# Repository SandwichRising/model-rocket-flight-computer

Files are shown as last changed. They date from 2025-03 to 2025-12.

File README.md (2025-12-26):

# Model Rocket Flight Control Computer
#### Servo-based flight control providing active stability and data logging for model rockets.

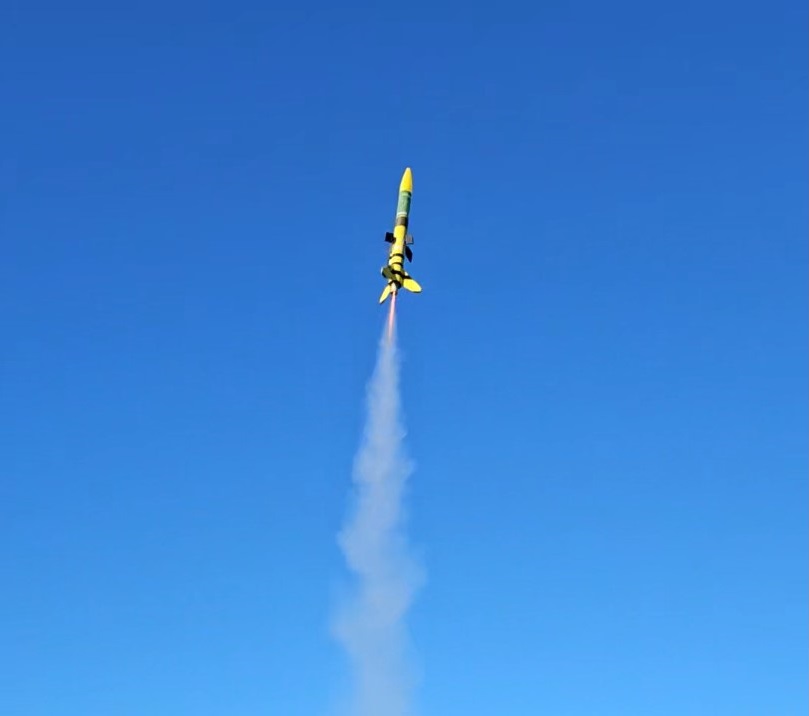
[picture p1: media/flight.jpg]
Model Rocket Flying


## Project Scope

This project is intended to provide hobbyists, academics, and model rocket teams with an understandable yet feature-rich open-source flight computer design utilizing servo-driven active stability and data logging capabilities. Block diagrams, schematics, source code, and engineering philosophies behind the design are all provided for anyone interested in model rocketry. Readily available consumer parts have been selected for the electronics and hobbyist rocket kits chosen with 3D-printed modifications added for ease of construction. The design is modular and made to be easily customized and edited, and also intended to be usable for steerable canards, tail fins, or thrust vector control (however, the latter two have not yet been tested). The implemented flight stability keeps the rocket pointed vertically by steering away from gravity, but does not allow any form of targeting or guidance to a target. 

To make this project hands-on and iterative, some unconventional decisions have been made that readers should be aware of, such as: choosing and constructing a theoretically conservative steering design using static modeling instead of fully modeling flight dynamics beforehand; using sensor fusion output that is not meant for thrust for the initial steering design, which is expected to need replacement under high-g forces; and using protoboard and CNC-milled PCB prototypes which are bulkier than factory-fabricated PCBs but allow rapid testing and design changes. It is my intent to continually analyze flight recordings to characterize the steering of different airframes and implement different state-space models to enhance the steering over time.

## Versioning

The project scope is divided into versions which contain an increasing number of features on varying rocket airframes. Currently, V1 and V2 are completed and have flight data recorded from numerous launches to analyze the active flight control behavior. Future versions with additional features are planned:

- V1 - ✓ - (Open-Source and Completed): Functional Flight Computer with BNO055 IMU, active vertical-flight steering fin control, and data logging to SD Card for flight analysis on a BT-60 Estes Green Eggs airframe. [An academic paper](https://ieeexplore.ieee.org/document/11267717) regarding the engineering of this V1 rocket has been published and presented at IEEE UEMCON 2025, which includes additional details.
- V2 - ⧗ - (Open-Source and Completed, Preparing GitHub Documentation): Barometer, battery charger, GPS, SDIO SD recording, LoRa, a ground station, and interrupt-driven steering added. A new 3-inch PCB and Apogee Mako rocket design were built and flown. 
- V3 - ☐ - (Undecided): 66mm rocket airframe with servo-controlled tail fins for additional data collection.
- V4 - ☐ - (Closed-Source): Fly-to-location and/or fly along trajectory features to simulate real-world requirements of high-powered rockets to exit the atmosphere and enter orbit along predetermined flight paths.

Later advanced versions of this flight computer software will be private and the source code will be closed. If you wish to collaborate on more advanced and legal rocket designs or custom-made computers for your use case, please feel free to contact me.  

#### V2 Rocket and Flight Computer
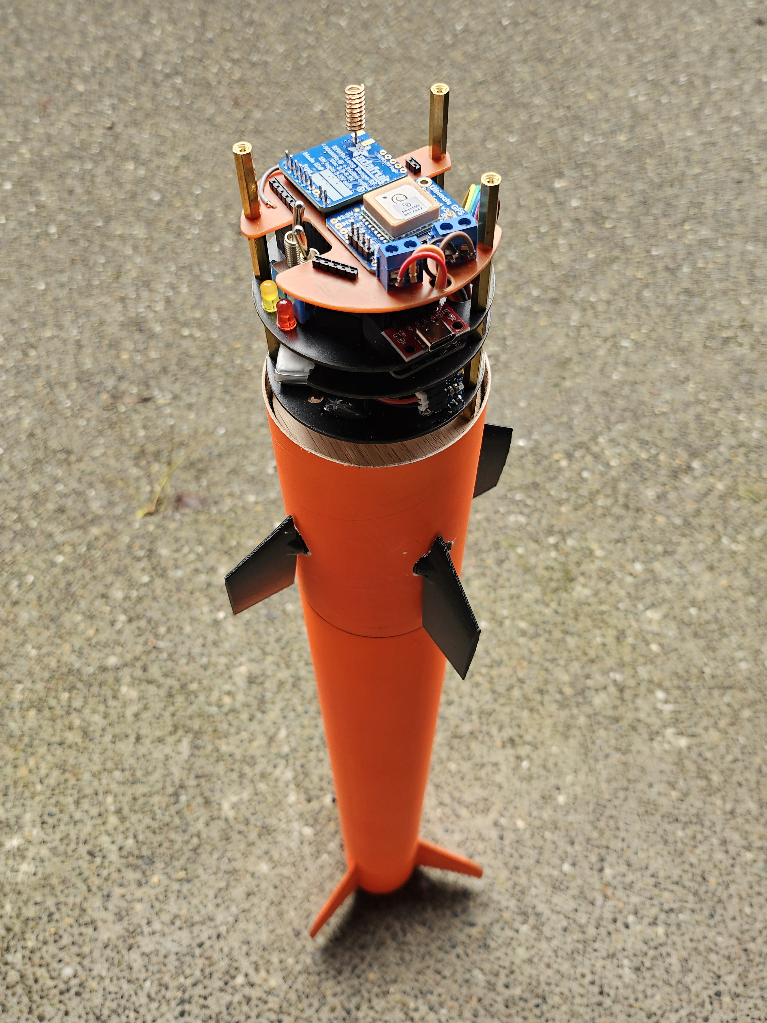
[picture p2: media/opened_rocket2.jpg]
V2 Partially Disassembled Model Rocket


## V1 Design Overview

The first milestone (V1) was to complete onboard flight control for vertical-up active flight guidance to continuously steer a model rocket directly away from Earth. This required creating a flight computer, flight computer software, and model rocket hardware. The flight computer hardware and software design blocks may be seen in the image below:

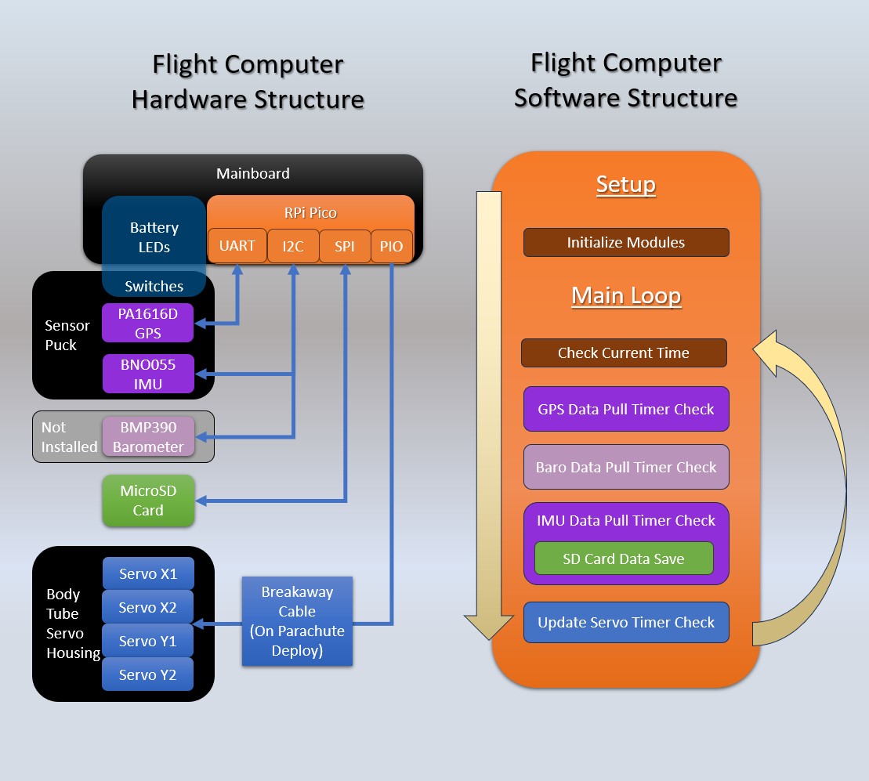
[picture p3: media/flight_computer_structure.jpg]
Flight Computer Structure

V1 Model Rocket

### V1 Flight Computer

Prior to designing and constructing the rocket, an RP2040 was selected to become the flight computer and a Pi Pico was implemented. A fast clock speed, multiple cores, and PIO ports were main considerations when selecting this microprocessor. The microprocessor was breadboarded with various sensors, an SD card, and servos. When software progressed far enough to provide proof of concept on breadboard, rocket construction began and the flight computer moved from a breadboard to a soldered protoboard and 3D-printed solution. Since the flight computer is 3.3v, a simple passive SD card to MicroSD adapter allowed jumper wires to be soldered directly to it in order to connect the flight computer directly to the MicroSD card used to log data. 

V1 Flight Computer

#### V1 and V2 Flight Computers
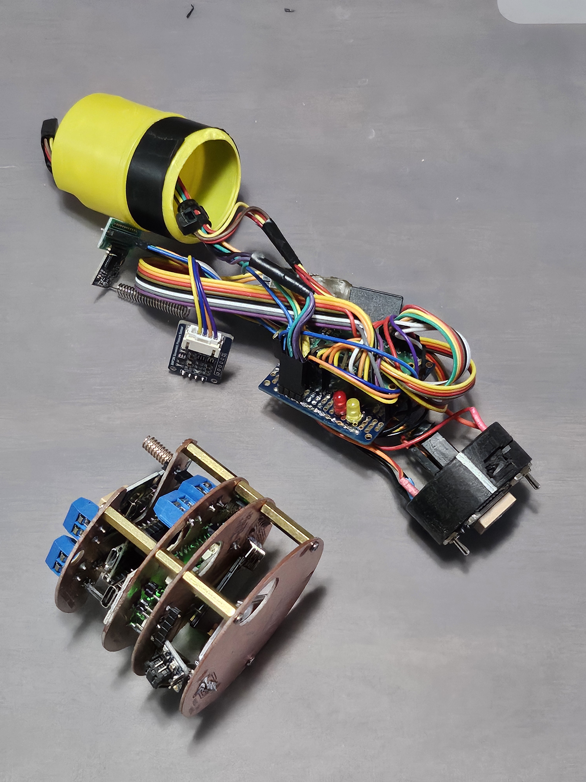
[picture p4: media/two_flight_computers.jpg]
V1 and V2 Flight Computers


### PIO Usage

The PIO ports of the RP2040 proved to be especially useful in servo control, as servos require exactly timed pulses in an approximate range of 1ms to 2ms to set their position. Using PIO, 4 state machines were created with their timings running independently of the core process without using interrupts, ensuring the fins will hold their exact set positions with consistent servo pulse timing regardless of the status of the main program. Positional changes of the fin are achieved by sending a new pulse timing delay to a corresponding servo's PIO register. Steering changes do require the core program to compute data and send updates, and therefore requires the processor to be looping through the program very quickly to provide smooth steering. V2 changes to the program involved moving the IMU polling and servo setting required to actively steer the rocket to an interrupt-driven program flow to provide continuously smooth active steering, regardless of the processor's looping speed.

To initially understand PIO implementation and the assembly code required to program it, active LED control was written for a yellow Status LED and red Recording LED as a PIO state machine program. The speed at which the LEDs flash gives the rocket operator insight into the rocket's current state and readiness for launch. As these LEDs are not time critical and can be easily controlled through polling in the main program, and only two different state machine programs may be implemented on an RP2040 at once, in later software versions this LED PIO state machine has been repurposed to accommodate D0-D3 SDIO style SD card saving, increasing the speed at which flight information can be saved.

### V1 Rocket Design

V1 of the rocket is built using a modified Estes Green Eggs model rocket kit. To establish the design, OpenRocket software was used to model simple flight characteristics of the rocket, such as Center of Gravity (CoG) and Center of Pressure (CoP), as well as to run simulations on expected flight dynamics with different Estes engines. An OpenRocket savefile containing a model of the stock Green Eggs rocket kit created by user BEC was downloaded from [rocketryforum.com](https://www.rocketryforum.com/threads/openrocket-or-rocksim-file-for-estes-green-eggs.182309/) and compared with the physical V1 rocket under construction. Minor adjustments to the existing design were made to match the V1's build, and then additional modules for flight control, sensors, and active steering were modeled into the design. As OpenRocket is designed with uncontrolled static-fin rockets in mind, steering dynamics could not be directly simulated. However, fin location vs Cog and CoP were observed for numerous modeled configurations and a design was decided on to test a flight control design implementation. 

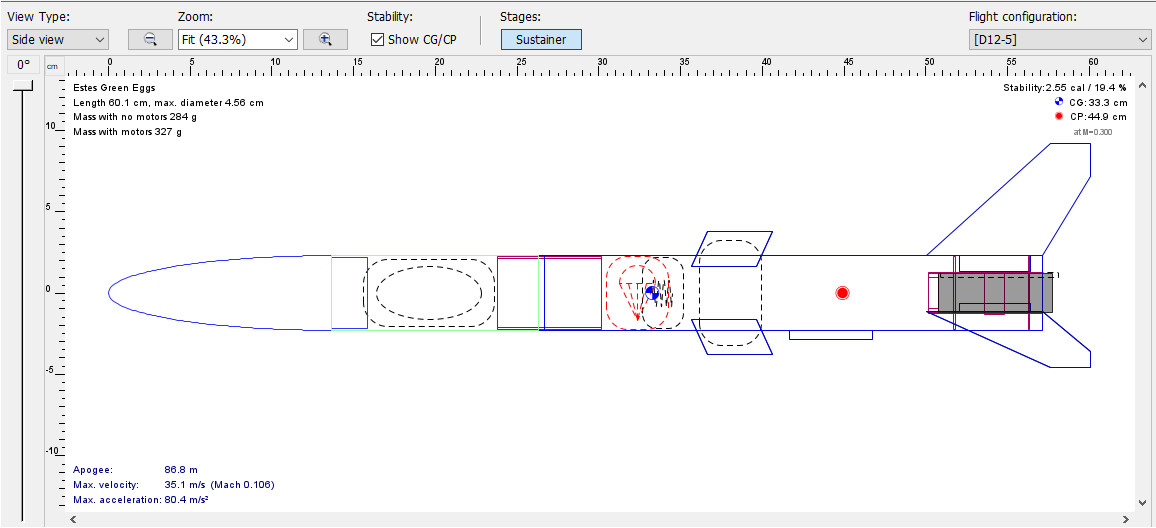
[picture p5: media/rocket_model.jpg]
Rocket Model


### V1 Servo Housing and Steering Fins

After modeling the flight characteristics and deciding on a location for servos and steering fins, a 3D model for a servo housing was created in Fusion360. A design for directly mounting the flight control fins to the servos without any additional linkage was decided on for simplicity and to save space. The servo housing is located between the engine and parachutes, requiring it to withstand the parachute ejection charge forces coming from the engine and allowing this force to pass through, ejecting the nose of the rocket and deploying the parachute without damaging the servos or housing. After deciding on servo positions in the housing, multiple vertical holes with beveling were added to the design to allow delivery of the parachute charge. This housing was then 3D-printed in PLA and permanently fixed inside the rocket's body tube using epoxy. The openings were cut out of the sides of the rocket body and the servos installed. The servo wires were routed vertically into the rocket body tube, and all the end connectors were removed. Two new and larger end connectors were used and fixed together to create a single break-away connector for all 4 servos. 

Steering fins were 3D modeled in Fusion360 to match the OpenRocket design used to model flight. Metal wires were glued into the center of the servo connector nubs to provide more support than just friction fitting the fin over the servo connector nubs. These semi-rigid wires pass all the way through the fin and are bent over at the tops of the fins to retain them and have proven effective in providing support, as fins have never come off in flight (but have in landing, and have been easily recovered in immediate proximity to the rocket and reinstalled without the glue being necessary). 

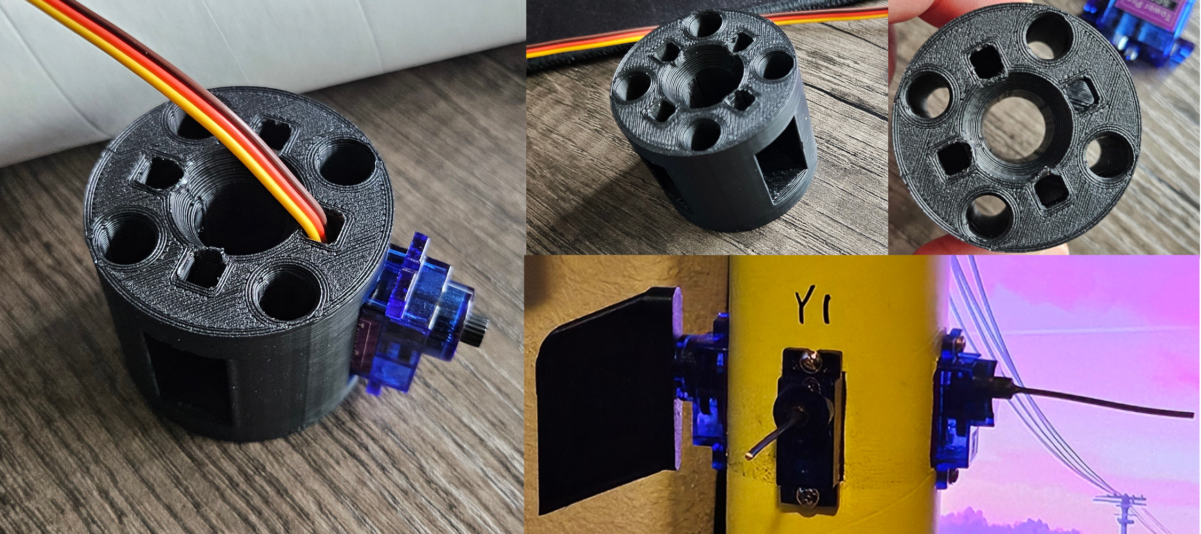
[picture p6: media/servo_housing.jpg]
Servo Housing


### V1 Sensor Puck

A puck-shaped sensor housing was designed in Fusion360 to house the BNO055 IMU and PA1616D GPS module. The sensor modules screw into the 3D-printed PLA housing and the entire assembly slides into the clear green tube holding the flight computer. The puck's shape ensures proper IMU sensor orientation and avoids sensor misalignment with the rocket. The GPS is positioned on the top of the puck (also above the flight computer) with a relatively unobstructed view of the sky to promote good signal reception. Two switches are also installed into the puck for user controls. One switch turns battery power to the flight computer on/off, and the other begins recording data to the SD card. Turning data recording off and then on again begins a new recording file. It would be ideal to add both a USB port and boot button for programming the RP2040 as well as access to the SD card through the top of the puck, however due to space constraints this may or may not be feasible in future revisions.

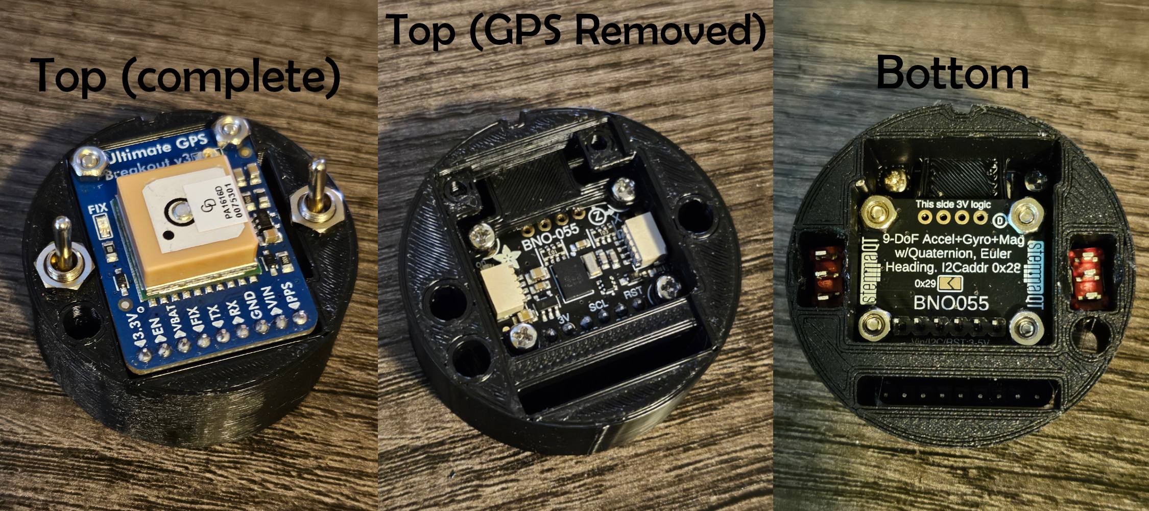
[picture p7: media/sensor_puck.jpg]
Sensor Puck


### V1 Flight Computer Software

The software is divided into two sections: PIO state machines and a main C program. The state machines and C program run independently of each other and interact through registers which change the behavior of the PIO state machines. In V1 the PIO state machines control the LEDs and servo pulses using a delay number, and each PIO state machine monitors its input register to accept a new delay number (in 125MHz clock ticks). The rest of the V1 software is a C program with polling-based timer design to retrieve data from sensors, record data to SD card, and set LED timing and servo positions through the PIO registers. Due to time constraints of getting V1 results only the BNO055 IMU, SD card, LEDs and Servos are fully implemented in V1. 

The BMP390 barometer planned for use has a complicated initialization process, and in V1 software enabling oversampling to improve data consistency currently prevents further data retrieval from the unit. Until the initialization coding for using the barometer is corrected, it remains physically uninstalled from the rocket.

The PA1616D GPS module is installed in the rocket's sensor puck and connected to the flight computer, however communication over UART with the GPS is relatively slow and must be parsed in full, instead of retrieving specific data on-demand as with the IMU. With the current V1 software implementation, receiving this GPS UART data causes the looping of the main C program to iterate slow enough to cause stuttering in the control fin steering. Due to potential steering stuttering, GPS data retrieval is currently disabled in V1. Planned fixes to this include moving the IMU data retrieval and steering fin PIO register control to an interrupt-based timer format, rather than polling. This will allow more freedom in dealing with slower loop iterations and parsing the UART data while having smooth steering control at all times. In addition, moving the UART parsing to an interrupt-based format may also be implemented to reduce polling UART when unnecessary. 

The SD card currently saves at 10Hz. More frequent logging is desired, however saving more often over SPI in V1 causes steering stuttering similar to using GPS UART. Interrupt-based solutions for IMU data and steering fin control are expected to help with this, and additionally moving from SPI-based saving to parallel D0-D3 SDIO communication through a PIO state machine should allow higher speed interface to the SD card. [carlk3's github library no-OS-FatFS-SD-SDIO-SPI-RPi-Pico](https://github.com/carlk3/no-OS-FatFS-SD-SDIO-SPI-RPi-Pico) is used to interface to the SD card over SPI and will continue to be used for SDIO interfacing. 

The BNO055 IMU in V1 is set to an NDOF mode, using a sensor fusion of the accelerometer, gyroscope, and magnetic sensor provided to a Kalman filter to output very stable data. This filtered data provides a gravity vector for each axis, which are used in steering. In an ideal vertical state, the gravity vector for the Z axis is 9.8, and the gravity vectors for both the X and Y axes are 0. This ideal state would have the rocket nose pointed straight away from the Earth. As the rocket tips sideways, the gravity vectors for X and Y increase/decrease and Z decreases. This non-ideal variation from 0 in X and Y is directly used to control the servo pulses for the related steering fins, correcting the rocket's flight to become more vertical. These gravity vectors, along with acceleration vectors, time, heading, and temperature are all collected from the IMU and saved to the SD card to later reconstruct the rocket flight path to analyze performance. 

It is important to note that while this steering method has been working on low-power rockets (currently up to 7.5 g), the BNO055 gravity vectors are not expected to remain reliable under more extreme acceleration. The BNO055 was not designed to be used under high thrust and a new filter method is expected to be necessary for high-powered flight. Out of curiosity, I will continue to push the sensor to its limits with an emphasis on maintaining safety during launches, while simultaneously developing new state-space models for steering to replace the sensor's built-in gravity vector method. 

The servos use a PIO assembly program which monitors the attached servo's state machine register for a delay number. This delay number is used to count down system clock ticks to produce a high pulse between approximately 1-2ms in duration, which corresponds to the two steering extremes of the servo. The countdown is then multiplied by 10 when the output goes low to generate a 100-200Hz high/low pulse cycle desirable for servo control. Once a delay is received, the state machine is able to deliver consistent pulse timing to the servos, completely independent of the C program, delivering consistent fin positioning regardless of overall program state. Only further steering changes are dependent on the C program writing new values to the state machine's input register. In V1, the LEDs use a very similar program to blink on and off at different speeds, informing the operator of program status.

## Collected Flight Data

At the time of this publication V1 has 9 flights logged, and V2 has 3 flights logged (and one more flight without electronics enabled). Using acceleration and gravity data without additional positional or altitude data has been problematic to reassemble into flight paths, but progress has been made. There is also unexpected IMU heading direction behavior at certain angles that needs to be understood and compensated for. Despite these difficulties, some flights have been successfully mapped by processing the acceleration, gravity, and heading data through MATLAB and then integrating into velocity and positional data. One flight path is shown modeled below, along with the OpenRocket simulation of the expected flight. While the rocket did not reach the full height modeled, the real-world data which was collected and mapped is still close to the simulated projection, with the parachute charge deploying very near apogee when expected.

With the inclusion of barometer data from V2 onward, the flights are becoming easier to map and characterize.

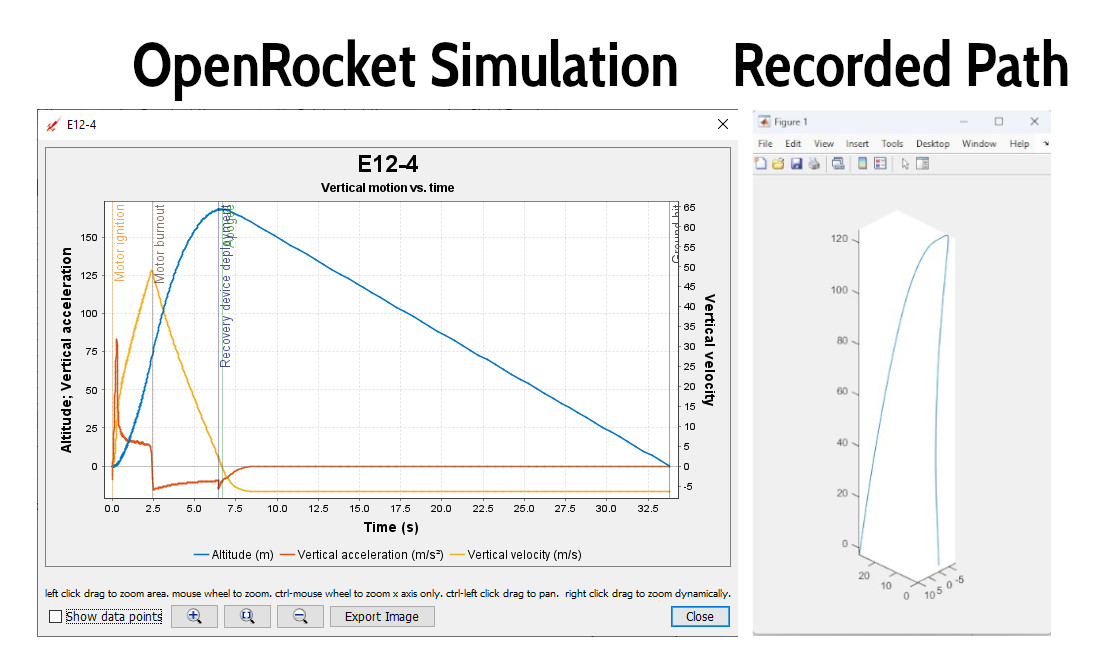
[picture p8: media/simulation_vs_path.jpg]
Simulation vs Recorded Path


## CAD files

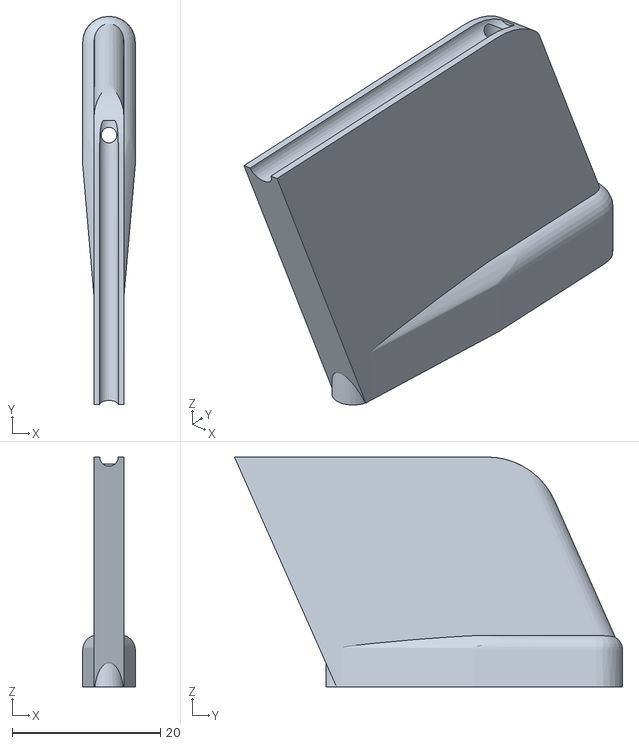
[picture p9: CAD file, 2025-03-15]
stls/Green_Eggs_Fin_with_Hole.stl
7.10 x 52.3 x 31.0

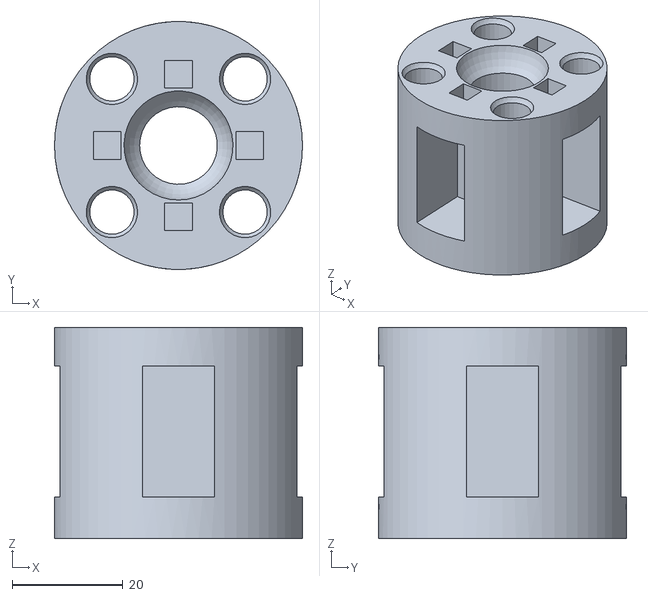
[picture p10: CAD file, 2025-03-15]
stls/Green_Eggs_Servo_Housing.stl
44.7 x 44.7 x 38.1

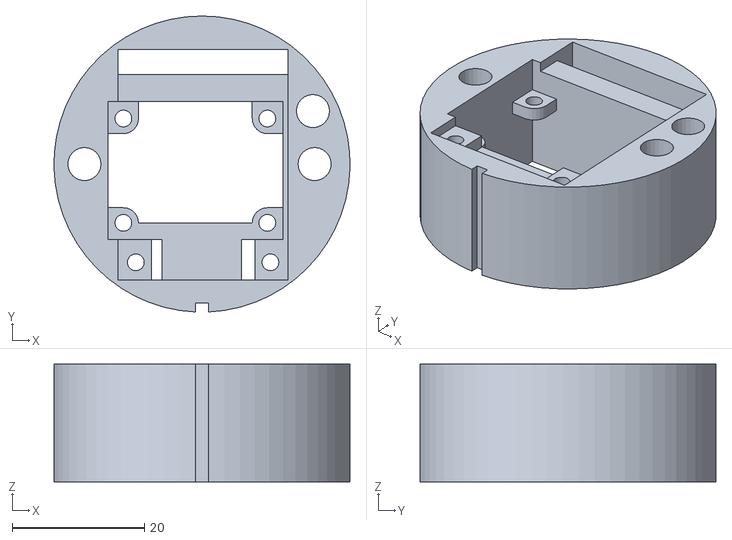
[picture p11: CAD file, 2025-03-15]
stls/Green_Eggs_Sensor_Puck.stl
44.7 x 44.7 x 17.8

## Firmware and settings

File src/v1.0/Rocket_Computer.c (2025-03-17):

/* 

    Model Rocket Flight Computer V1.0 - GNU GPLv3
    Active steering control for vertical-directed flight

    Working code, WIP. No guarantees or warranty implied.
    Rocketry has inherent danger, use at own risk.

    Hardware Implement:
    [X] Servo PIO Control
    [X] BNO055 IMU Data
    [X] SPI SD Card Record
    [ ] PA1616D GPS Data - UART speed interferes with steering
    [ ] BMP390 Baro Data - init code incomplete

    Next Feature Improvements:
    [ ] Interrupt-driven IMU and servos
    [ ] PIO SDIO SD Card + Polling LED

    Note: carlk3's github library is used to interface to the SD card:
    https://github.com/carlk3/no-OS-FatFS-SD-SDIO-SPI-RPi-Pico

*/

#include <stdio.h>
#include <math.h>
#include "pico/stdlib.h"
#include "pico/time.h"
#include "hardware/i2c.h"
#include "hardware/pio.h"
#include "hardware/uart.h"
#include "blink.pio.h"
#include "hw_config.h"
#include "f_util.h"
#include "ff.h"

// initialize and poll modules on/off
#define SET_SERVOS true
#define GET_IMU true
#define RECORD_IMU true
#define GET_GPS false
#define GET_BARO false

#define PIO_LED // comment in/out to turn on/off PIO LED state machine

// turn on/off debugging code 
//#define DEBUG_MODE   // comment in to compile/display cycles per second
//#define DEBUG_PRINTS // comment in to compile and send print statements
#define PRINT_IMU false  // t/f to allow IMU serial printout
//#define PRINT_GPS true etc...

// I2C defines
#define I2C_PORT i2c1
#define I2C_SDA 14
#define I2C_SCL 15
#define BN0_ADDY 0x28  // IMU
#define BMP_ADDY 0x77  // barometer

// UART defines
// By default the stdout UART is `uart0`, so we will use the second one
#define GPS_UART_ID uart1
//#define GPS_BAUD_RATE 115200
#define GPS_BAUD_RATE 9600
//#define GPS_BAUD_RATE 38400
#define UART_TX_PIN 8
#define UART_RX_PIN 9


// recording pin and filename defines
#define RECORDING_PIN 1
// SD Card Filename builders
const char filenameIMUbegin[] = "IMU_";
const char filenameIMUextension[] = ".csv";

#define RECORD_LED_PIN 6
#define STATUS_LED_PIN 7

#define SERVO_X1_PIN 2
#define SERVO_X2_PIN 3
#define SERVO_Y1_PIN 4
#define SERVO_Y2_PIN 5
// servo midpoint and steps (times gravity vectors 0-9.8) in 125MHz clock ticks
#define SERVO_MIDPOINT 187500 
//#define SERVO_STEP 4000 // first two flights at this value
#define SERVO_STEP 7000   // higher response than previous
#define SERVO_X1_OFFSET 0
#define SERVO_X2_OFFSET 0
#define SERVO_Y1_OFFSET 0
#define SERVO_Y2_OFFSET 0

// polling timer delays (in ms)
#define SERVO_DELAY 10
#define IMU_DELAY 10
#define RECORD_DELAY 100 // nested inside IMU delay, can't be faster
#define GPS_DELAY 5
#define BARO_DELAY 10


// init IMU function
void bno055_init (void) {

    // wait for IMU to initialize
    sleep_ms(1000); 
    // pull chip ID and compare with expected ID
    uint8_t IDreg = 0x00;
    uint8_t chipID[1];
    i2c_write_blocking(I2C_PORT, BN0_ADDY, &IDreg, 1, true);
    i2c_read_blocking(I2C_PORT, BN0_ADDY, chipID, 1, false);

    if (chipID[0] != 0xA0) {
        while(1){
            #ifdef DEBUG_PRINTS 
                printf("BNO055 Chip ID Not Correct - Check Connection!\n");
            #endif
            sleep_ms(5000);
        }
    }    
    
    // use external oscillator and reset
    uint8_t data[2];
    data[0] = 0x3F;
    data[1] = 0x40;
    i2c_write_blocking(I2C_PORT, BN0_ADDY, data, 2, true);

    // Reset all interrupt status bits
    data[0] = 0x3F;
    data[1] = 0x01;
    i2c_write_blocking(I2C_PORT, BN0_ADDY, data, 2, true);

    /*
    // Configure Power Mode
    data[0] = 0x3E;
    data[1] = 0x00;
    i2c_write_blocking(I2C_PORT, BN0_ADDY, data, 2, true);
    sleep_ms(50);
    */

    // Default Axis Configuration
    data[0] = 0x41;
    data[1] = 0x24;
    i2c_write_blocking(I2C_PORT, BN0_ADDY, data, 2, true);

    // Default Axis Signs
    data[0] = 0x42;
    data[1] = 0x00;
    i2c_write_blocking(I2C_PORT, BN0_ADDY, data, 2, true);

    // set units to windows, fahrenheit, and m/s^2
    data[0] = 0x3B;
    data[1] = 0x00;
    i2c_write_blocking(I2C_PORT, BN0_ADDY, data, 2, true);
    sleep_ms(30);

    // set operation to NDOF
    data[0] = 0x3D;
    data[1] = 0x0C;
    i2c_write_blocking(I2C_PORT, BN0_ADDY, data, 2, true);
    sleep_ms(100);

    #ifdef DEBUG_PRINTS 
        printf("BNO055 Initialized.\n");
    #endif

}



// init barometer function
void bmp390_init (void) {

    // wait for barometer to initialize
    sleep_ms(1000); 
    // pull chip ID and compare with expected ID
            
    uint8_t IDreg = 0x00;
    uint8_t chipID[1];

    i2c_write_blocking(I2C_PORT, BMP_ADDY, &IDreg, 1, true);
    i2c_read_blocking(I2C_PORT, BMP_ADDY, chipID, 1, false);

    if (chipID[0] != 0x60) {
        while(1){
            #ifdef DEBUG_PRINTS 
                printf("BMP390 Chip ID Not Correct - Check Connection!\n");
            #endif
            sleep_ms(5000);
        }
    }    

    uint8_t data[2];
    
    // Configure FIFO
    data[0] = 0x17;
    data[1] = 0x00; // disable
    i2c_write_blocking(I2C_PORT, BMP_ADDY, data, 2, true);
    sleep_ms(50);

    // Configure Power Mode (normal, on pres, on temp)
    data[0] = 0x1B;
    data[1] = 0x33;
    i2c_write_blocking(I2C_PORT, BMP_ADDY, data, 2, true);
    sleep_ms(50);

    // Configure Oversampling
    data[0] = 0x1C;
    data[1] = 0x00; //  no oversample
    //data[1] = 0x0C; //  16x baro, 2x temp
    //data[1] = 0x0D; //  32x baro, 2x temp
    i2c_write_blocking(I2C_PORT, BMP_ADDY, data, 2, true);
    sleep_ms(50);

    // Configure Data Rate (200Hz)
    data[0] = 0x1D;
    //data[1] = 0x00; // 200Hz
    data[1] = 0x01; // 100Hz
    //data[1] = 0x02; // 50Hz
    //data[1] = 0x07; // 640ms
    i2c_write_blocking(I2C_PORT, BMP_ADDY, data, 2, true);
    sleep_ms(50);

    // Configure IIR Filter
    data[0] = 0x1F;
    data[1] = 0x00; // bypass
    //data[1] = 0x03; // coef_7
    //data[1] = 0x05;
    //data[1] = 0x07; // coef_127
    i2c_write_blocking(I2C_PORT, BMP_ADDY, data, 2, true);
    sleep_ms(50);
    #ifdef DEBUG_PRINTS 
        printf("BMP390 Initialized.\n");
    #endif

}

void blink_pin_forever(PIO pio, uint sm, uint offset, uint pin, uint freq) {
    blink_program_init(pio, sm, offset, pin);
    pio_sm_set_enabled(pio, sm, true);

    // modified blink example
    // PIO counter program takes 3 more cycles in total than we pass as
    // input (wait for n + 1; mov; jmp)
    pio->txf[sm] = (125000000 / (2 * freq)) - 3;
}


void servo(PIO pio, uint sm, uint offset, uint pin, uint freq) {
    blink_program_init(pio, sm, offset, pin);
    pio_sm_set_enabled(pio, sm, true);

    pio->txf[sm] = SERVO_MIDPOINT; // mid
}

int main()
{
    stdio_init_all();

    //SD Card vars
    FRESULT fr;
    FATFS fs;
    FIL fil;
    int ret;
    char buf[100];
    bool recording = false;
    bool recordingWasOn = false;
    uint8_t fileIncrement = 1;
    
    // Recording switch init
    gpio_init(RECORDING_PIN);
    gpio_set_dir(RECORDING_PIN, GPIO_IN);
    gpio_pull_up(RECORDING_PIN);
    
    uint offset;

    #ifdef PIO_LED
        // PIO LED Blinking (status and recording LEDs)
        PIO pioLED = pio0;
        offset = pio_add_program(pioLED, &blink_program);
        //printf("Loaded program at %d\n", offset);
        blink_pin_forever(pioLED, 0, offset, STATUS_LED_PIN, 3);
        blink_pin_forever(pioLED, 1, offset, RECORD_LED_PIN, 3);
    #endif
    
    // servo control PIO init
    PIO pioServo = pio1;
    offset = pio_add_program(pioServo, &blink_program);
    //printf("Loaded program at %d\n", offset);
    servo(pioServo, 0, offset, SERVO_X1_PIN, 3); // X1
    servo(pioServo, 1, offset, SERVO_X2_PIN, 3); // X2
    servo(pioServo, 2, offset, SERVO_Y1_PIN, 3); // Y1
    servo(pioServo, 3, offset, SERVO_Y2_PIN, 3); // Y2

    // I2C initialization. Using it at 400Khz (BNO055 max).
    i2c_init(I2C_PORT, 400*1000);
    gpio_set_function(I2C_SDA, GPIO_FUNC_I2C);
    gpio_set_function(I2C_SCL, GPIO_FUNC_I2C);
    gpio_pull_up(I2C_SDA);
    gpio_pull_up(I2C_SCL);

    // initialize BNO055
    if (GET_IMU) bno055_init();
    // initialize BMP390
    if (GET_BARO) bmp390_init();

    // initialize UART (GPS)
    uart_init(GPS_UART_ID, GPS_BAUD_RATE);
    //uart_init(UART_ID, 9600);
    gpio_set_function(UART_TX_PIN, GPIO_FUNC_UART);
    gpio_set_function(UART_RX_PIN, GPIO_FUNC_UART);
    //uart_set_format(UART_ID, 8, 1, UART_PARITY_NONE);
    sleep_ms(500);

    // OPTIONAL GPS SETTINGS (baud rate settings)
    // In a default system, printf will also output via the default UART
    // uart_puts(GPS_UART_ID, "$PMTK251,38400*27");
    // uart_puts(UART_ID, "$PMTK251,115200*1F\r\n");
    // uart_puts(UART_ID, "$PMTK251,0*28\r\n"); // default setting
    // uart_putc(UART_ID, 0x0D);
    // uart_putc(UART_ID, 0x0A);

    //SD TEST
    if (RECORD_IMU){
        // Initialize SD card
        if (!sd_init_driver()) {
            #ifdef DEBUG_PRINTS 
                printf("ERROR: Could not initialize SD card\r\n");
            #endif
            while (true);
        }

        // Mount drive
        fr = f_mount(&fs, "0:", 1);
        if (fr != FR_OK) {
            #ifdef DEBUG_PRINTS 
                printf("ERROR: Could not mount filesystem (%d)\r\n", fr);
            #endif
            while (true);
        }
    }

    #ifdef PIO_LED
        // INIT COMPLETE - change LED blink speed
        pio0->txf[0] = (1250000000 / (2 * 3)) - 3; // status slow blink
        pio0->txf[1] = 0; // recording led off
    #endif
    
    // init global variables
    // IMU
    uint8_t accel[6]; // pull location for 6 acceleration registers from IMU
    uint8_t grav[6]; // pull location for 6 gravity registers from IMU
    uint8_t head[2]; // pull location for 2 heading registers from IMU
    uint8_t mag[2]; // pull location for 2 heading registers from IMU
    int8_t temperatureIMU; // pull location for IMU temperature register from IMU
    int16_t accelX, accelY, accelZ, heading, gravX, gravY, gravZ, magnetoZ; // combined 3-axis data
    float f_accelX, f_accelY, f_accelZ, f_gravX, f_gravY, f_gravZ, f_heading, f_temperatureIMU;
    uint8_t accelRegStart = 0x08; //start address of accel registers
    uint8_t magRegStart = 0x12; //start address of magnetometer Z registersa
    uint8_t headRegStart = 0x1A; //start address of heading register
    uint8_t gravRegStart = 0x2E; //start address of gravity vector register
    uint8_t tempRegStart = 0x34; //start address of IMU temperature register
    // baro
    uint8_t pressure[3]; // pull location for 3 pressure registers from baro
    uint8_t temperature[3]; // pull location for 3 pressure registers from baro
    uint32_t pressureData;
    uint32_t temperatureData;
    float f_altitudeData, f_pressureData, f_temperatureData;
    uint8_t  baroRegStart = 0x04; //start address of barometer registers (pressure)
    uint8_t  baroRegStart2 = 0x07; //start address of barometer registers (temperature)


    #ifdef DEBUG_MODE
        //debug helpers
        uint32_t CPS = 0;
        uint32_t CPS_timer = to_ms_since_boot(get_absolute_time());
    #endif

    // global loop ms timers (slightly staggered)
    uint32_t currentTime = 0;
    uint32_t uartTimer = 1;
    uint32_t accelTimer = 2;
    uint32_t recordTimer = 2;
    uint32_t baroTimer = 3;
    uint32_t servoTimer = 4;


    // MAIN LOOP
    while (true) {

        currentTime = to_ms_since_boot(get_absolute_time());

        // read gps uart
        if (GET_GPS && (uartTimer + GPS_DELAY <= currentTime)) {
            if (uart_is_readable(GPS_UART_ID)){
                char holding[2];
                uart_read_blocking(GPS_UART_ID, holding, 2);
                #ifdef DEBUG_PRINTS 
                    printf(holding);
                #endif
            }
            uartTimer = currentTime;
            //printf("\n");
        }

        #ifdef DEBUG_MODE
            // debug Cycles Per Second
            CPS += 1;
            if (CPS_timer + 1000 <= currentTime) {
                printf("\n");
                printf("Cycles Per Second: %d\n", CPS);
                CPS = 0;
                CPS_timer = currentTime;
            }
        #endif

        // pull IMU data
        if (GET_IMU && (accelTimer + IMU_DELAY <= currentTime)) {
            
            i2c_write_blocking(I2C_PORT, BN0_ADDY, &accelRegStart, 1, true);
            i2c_read_blocking(I2C_PORT, BN0_ADDY, accel, 6, false);
            accelX = ((accel[1]<<8) | accel[0]);
            accelY = ((accel[3]<<8) | accel[2]);
            accelZ = ((accel[5]<<8) | accel[4]);
            f_accelX = accelX / 100.00;
            f_accelY = accelY / 100.00;
            f_accelZ = (accelZ / 100.00); 

            i2c_write_blocking(I2C_PORT, BN0_ADDY, &gravRegStart, 1, true);
            i2c_read_blocking(I2C_PORT, BN0_ADDY, grav, 6, false);
            gravX = ((grav[1]<<8) | grav[0]);
            gravY = ((grav[3]<<8) | grav[2]);
            gravZ = ((grav[5]<<8) | grav[4]);
            f_gravX = gravX / 100.00;
            f_gravY = gravY / 100.00;
            f_gravZ = gravZ / 100.00;

            i2c_write_blocking(I2C_PORT, BN0_ADDY, &headRegStart, 1, true);
            i2c_read_blocking(I2C_PORT, BN0_ADDY, head, 2, false);
            heading = ((head[1]<<8) | head[0]);
            f_heading = heading / 16.00; 
            
            i2c_write_blocking(I2C_PORT, BN0_ADDY, &tempRegStart, 1, true);
            i2c_read_blocking(I2C_PORT, BN0_ADDY, &temperatureIMU, 1, false);
            f_temperatureIMU = (temperatureIMU * (9.0/5.0)) + 32; 

           
            i2c_write_blocking(I2C_PORT, BN0_ADDY, &magRegStart, 1, true);
            i2c_read_blocking(I2C_PORT, BN0_ADDY, mag, 2, false); 
            magnetoZ = ((mag[1]<<8) | mag[0]);

            #ifdef DEBUG_PRINTS 
                if (PRINT_IMU) {
                    //printf("%d %d %d %d %d %d\n", accel[0], accel[1], accel[2], accel[3], accel[4], accel[5]);
                    //printf("X: %d    Y: %d    Z: %d\n", accelX, accelY, accelZ);
                    printf("X: %6.2f    Y: %6.2f    Z: %6.2f\n", f_accelX, f_accelY, f_accelZ);
                    printf("GrX: %6.2f    GrY: %6.2f    GrZ: %6.2f\n", f_gravX, f_gravY, f_gravZ);
                    printf("Heading: %6.2f    Temp: %d*C / %3.0f*F  Mag: %d\n", f_heading, temperatureIMU, f_temperatureIMU, magnetoZ);
                }
            #endif

            // manual debugging code
            // printf("Heading: %6.2f  Mag: %d\n", f_heading,  magnetoZ);

            recording = !gpio_get(RECORDING_PIN);

            // set recording led/filename based on switch position
            if (RECORD_IMU && (recording != recordingWasOn)) {
                if (recording) {

                    // PREPARE FILE
                    char num[10];
                    bool fileReady = false;

                    while (!fileReady){

                        // build filename from variable
                        sprintf(num, "%d", fileIncrement);
                        strcpy(buf, filenameIMUbegin);
                        strcat(buf, num);
                        strcat(buf, filenameIMUextension);

                        // debug print
                        //printf("Constructing filename: ");
                        //printf(buf);
                        //printf("\n");

                        // check if file + csv header needs created
                        fr = f_open(&fil, buf, FA_OPEN_EXISTING);
                        if (fr == FR_NO_FILE){
                            f_open(&fil, buf,  (FA_WRITE | FA_CREATE_NEW));
                            f_printf(&fil, "Time(ms), AccelX, AccelY, AccelZ, GravX, GravY, GravZ, Heading, Temp (*C)\r\n");
                            fileReady = true;
                            // debug print
                            //printf("File doesn't exist, new file created...\n");

                        // continuous record or increment filename if making a new record
                        } else if ((fr == FR_OK) && recordingWasOn){
                            fileReady = true;
                            // debug print
                            //printf("Already recording, Continue Record...\n");
                        } else if ((fr == FR_OK) && !recordingWasOn){
                            f_close(&fil);
                            fileIncrement += 1;
                            // debug print
                            //printf("Filename used by another recording, increment filename...\n");
                        }
                        
                    }
                    // Close file
                    f_close(&fil);



                    #ifdef PIO_LED
                        pio0->txf[1] = (1250000000 / (2 * 3)) - 3; // record status LED slow blink
                    #endif
                }


                #ifdef PIO_LED
                    else pio0->txf[1] = 0; // record status LED off
                #endif
            } 


            // actively record data
            if (RECORD_IMU && recording && (recordTimer + RECORD_DELAY <= currentTime)) {

                // debug print
                //printf("Begin Data Logging...\n");

                // RECORD DATA
                // Open file for appending data
                f_open(&fil, buf, FA_WRITE);
                // Seek to end
                f_lseek(&fil, f_size(&fil));
                // Write something to file
                f_printf(&fil, "%lu, %6.2f, %6.2f, %6.2f, %6.2f, %6.2f, %6.2f, %6.2f, %d\r\n", 
                    currentTime, f_accelX, f_accelY, f_accelZ, f_gravX, f_gravY, f_gravZ, f_heading, temperatureIMU);
                //f_printf(&fil, "%6.2f, %6.2f, %6.2f, ", f_accelX, f_accelY, f_accelZ); // accelerations
                //f_printf(&fil, "%6.2f, %6.2f, %6.2f, ", f_gravX, f_gravY, f_gravZ); //gravities
                //f_printf(&fil, "%6.2f, %d\r\n", f_heading, temperatureIMU); // heading, temperature
                // Close file
                f_close(&fil);
                
                // debug print 
                //printf("Record Saved.\n");

                recordTimer = currentTime;
            }
            
            recordingWasOn = recording;
            accelTimer = currentTime;
        }

        
        // pull barometer data
        if (GET_BARO && (baroTimer + BARO_DELAY <= currentTime)) {
            
            i2c_write_blocking(I2C_PORT, BMP_ADDY, &baroRegStart, 1, true);
            i2c_read_blocking(I2C_PORT, BMP_ADDY, &pressure[0], 3, false);
            i2c_write_blocking(I2C_PORT, BMP_ADDY, &baroRegStart2, 1, true);
            i2c_read_blocking(I2C_PORT, BMP_ADDY, &temperature[0], 3, false);

            //pressureData = ((pressure[0] & 0x1F)<<16 | pressure[1]<<8 | pressure[2]); // 21 bits @ 32x oversample
            //f_pressureData = pressureData * 0.085; // 21bit = 0.085 Pa per bit
            pressureData = (pressure[2]<<8 | pressure[1]); // 16 bits @ no oversample
            f_pressureData = pressureData * 2.64; // 16bit = 2.64 Pa per bit
            //temperatureData = ((temperature[0] & 0x01)<<16 | temperature[1]<<8 | temperature[2]); // 17 bits @ 2x oversample
            //f_temperatureData = temperatureData / 400.0; // 17bit = 0.0025 C per bit
            temperatureData = (temperature[2]<<8 | temperature[1]); // 16 bits @ no oversample
            f_temperatureData = temperatureData * 0.0007; // 16bit = 0.005 C per bit
            f_altitudeData = 44330.0 * (1.0 - pow(((f_pressureData / 100.0) / 1013.25), 0.1903));  // 1013.25 hPa at sea level
            
            #ifdef DEBUG_PRINTS 
                //printf("Baro pressure: %d, %d, %d  temperature: %d, %d, %d \n", pressure[0], pressure[1], pressure[2], temperature[0], temperature[1], temperature[2]);
                printf("Baro pressure: %6.2f  temperature: %6.2f altitude: %6.2f\n", f_pressureData, f_temperatureData, f_altitudeData);
            #endif

            baroTimer = currentTime;

        }

        
        // update servo positioning
        if (SET_SERVOS && (servoTimer + SERVO_DELAY <= currentTime)) {
            
            int32_t finPos[4];

            if(f_gravX >= -9.8 && f_gravX <= 9.8) {
                //X1
                finPos[0] = (f_gravX * SERVO_STEP) + SERVO_MIDPOINT + SERVO_X1_OFFSET;
                pio1->txf[0] = finPos[0];
                //X2
                finPos[1] = (f_gravX * SERVO_STEP * -1) + SERVO_MIDPOINT + SERVO_X2_OFFSET;
                pio1->txf[1] = finPos[1];
            }
            if(f_gravY >= -9.8 && f_gravY <= 9.8) {
                //Y1
                finPos[2] = (f_gravY * SERVO_STEP) + SERVO_MIDPOINT + SERVO_Y1_OFFSET;
                pio1->txf[2] = finPos[2];
                //Y2
                finPos[3] = (f_gravY * SERVO_STEP * -1) + SERVO_MIDPOINT + SERVO_Y2_OFFSET;
                pio1->txf[3] = finPos[3];
            }

            servoTimer = currentTime;
        }

    }
}

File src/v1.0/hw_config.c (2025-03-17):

/* hw_config.c
Copyright 2021 Carl John Kugler III

Licensed under the Apache License, Version 2.0 (the License); you may not use
this file except in compliance with the License. You may obtain a copy of the
License at

   http://www.apache.org/licenses/LICENSE-2.0
Unless required by applicable law or agreed to in writing, software distributed
under the License is distributed on an AS IS BASIS, WITHOUT WARRANTIES OR
CONDITIONS OF ANY KIND, either express or implied. See the License for the
specific language governing permissions and limitations under the License.
*/

/*
This file should be tailored to match the hardware design.

See
https://github.com/carlk3/no-OS-FatFS-SD-SDIO-SPI-RPi-Pico/tree/main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
*/

#include "hw_config.h"

/* Configuration of hardware SPI object */
static spi_t spi = {    
    .hw_inst = spi1,  // SPI component
    .sck_gpio = 10,    // GPIO number (not Pico pin number)
    .mosi_gpio = 11,
    .miso_gpio = 12,
    //.baud_rate = 125 * 1000 * 1000 / 8  // 15625000 Hz
    //.baud_rate = 125 * 1000 * 1000 / 6  // 20833333 Hz
    //.baud_rate = 125 * 1000 * 1000 / 4  // 31250000 Hz
    .baud_rate = 125 * 1000 * 1000 / 3    // 41666666 Hz
    //.baud_rate = 125 * 1000 * 1000 / 2  // 62500000 Hz
};

/* SPI Interface */
static sd_spi_if_t spi_if = {
    .spi = &spi,  // Pointer to the SPI driving this card
    .ss_gpio = 13  // The SPI slave select GPIO for this SD card
};

/* Configuration of the SD Card socket object */
static sd_card_t sd_card = {
    .type = SD_IF_SPI,
    .spi_if_p = &spi_if  // Pointer to the SPI interface driving this card
};

/* ********************************************************************** */

size_t sd_get_num() { return 1; }

/**
 * @brief Get a pointer to an SD card object by its number.
 *
 * @param[in] num The number of the SD card to get.
 *
 * @return A pointer to the SD card object, or @c NULL if the number is invalid.
 */
sd_card_t *sd_get_by_num(size_t num) {
    if (0 == num) {
        // The number 0 is a valid SD card number.
        // Return a pointer to the sd_card object.
        return &sd_card;
    } else {
        // The number is invalid. Return @c NULL.
        return NULL;
    }
}

/* [] END OF FILE */
